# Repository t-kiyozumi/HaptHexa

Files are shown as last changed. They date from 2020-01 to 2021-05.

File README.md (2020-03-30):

# HaptHexa
The contents of this repository are the source code and design drawing of a 6-legged robot that can be operated using Dual Shock 3.

#Installation，How to use

Assemble the robot with reference to
HaptHexa / Hardware.

Clone the repository to the computer that controls the robot.

Create a build folder in 
HaptHexa / Software / mainDirectory /

After connecting the dual shock3 controller to the robot's control computer, 
enter the following command to execution

./HaptHexa

Use the left stick to move and the right stick to control the posture.
Pressing select activates the stabilizer and tries to keep the posture horizontal.
In this state, the right stick is used to control the center of gravity.

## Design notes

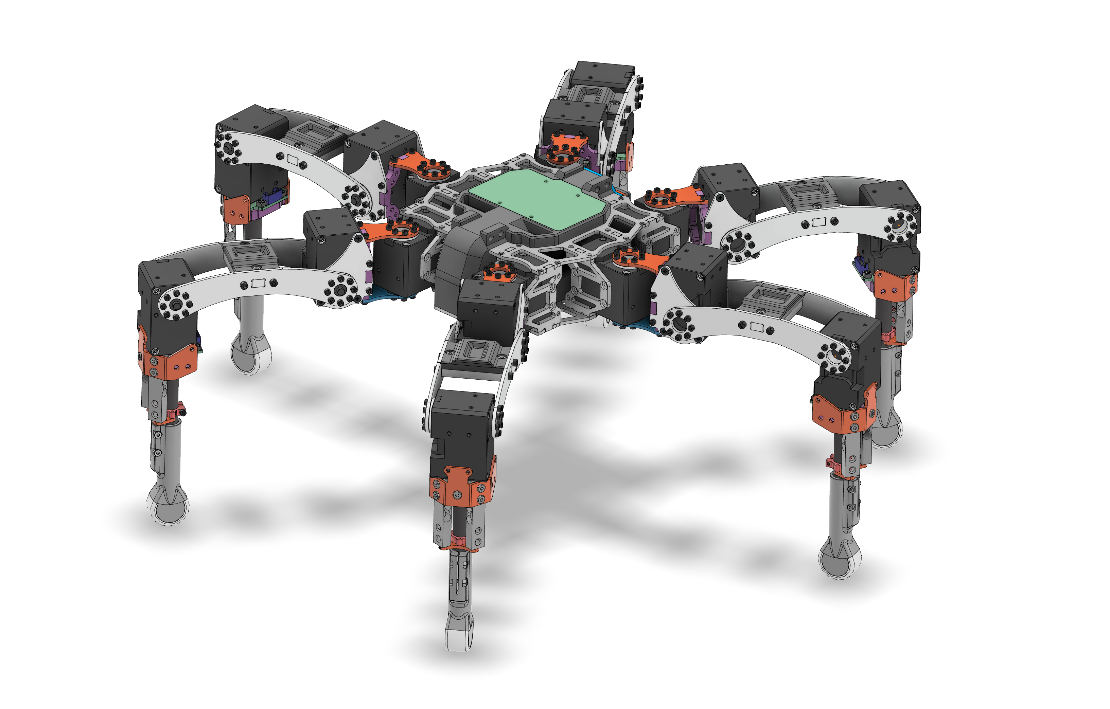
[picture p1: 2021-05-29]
Hardware/Inventor/00_000_HAPTHEXA_R3.png

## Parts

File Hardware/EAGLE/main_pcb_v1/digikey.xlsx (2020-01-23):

索引 | 数量 | 品番 | メーカー品番 | 商品概要 | 客先参照品番 | 入手可能 | 繰越注文 | 単価 | 合計金額 JPY
1 | 10 | WM1848-ND | 0436450500 | CONN RECEPT 5POS 3MM SINGLE ROW |  | 10 | 0 | 46.9 | 469
2 | 4 | WM1898CT-ND | 0436500513 | CONN HEADER 5POS R/A W/NAIL SMD |  | 4 | 0 | 344 | 1376
3 | 50 | WM1125CT-ND | 0430300002 | CONN TERM FEMALE 20-24AWG GOLD |  | 50 | 0 | 14.28 | 714

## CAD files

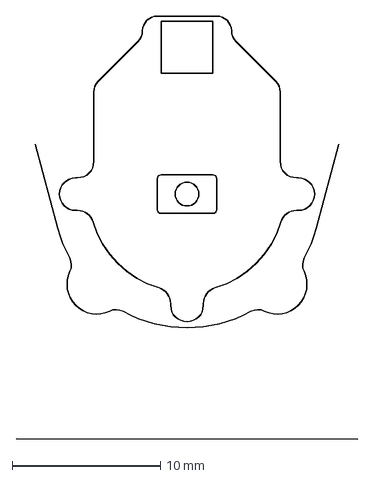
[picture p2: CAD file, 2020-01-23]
Hardware/EAGLE/force_sensor_pcb_v2/dxf/tplace_v2.dxf
23.0 x 28.5 mm

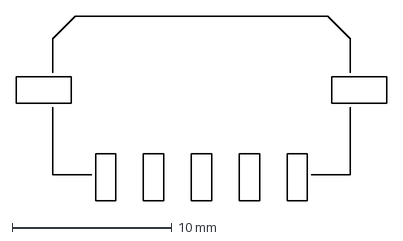
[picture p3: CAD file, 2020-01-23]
Hardware/EAGLE/main_pcb_v1/dxf/micro-fit 5.dxf
23.2 x 11.5 mm

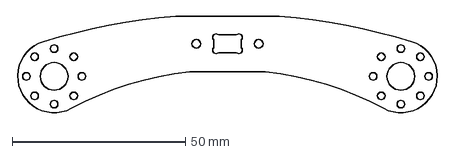
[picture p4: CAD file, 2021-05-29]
Hardware/Inventor/FEMUR_FRAME_DRIVER.dxf
122.0 x 28.5 mm

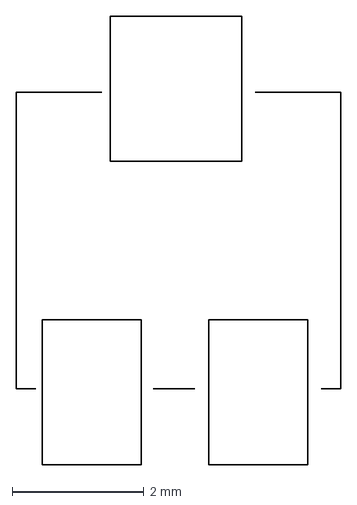
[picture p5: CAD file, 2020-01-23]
Hardware/EAGLE/force_sensor_pcb_v2/dxf/TOCOS G43A FOOTPRINT.dxf
4.92 x 6.80 mm

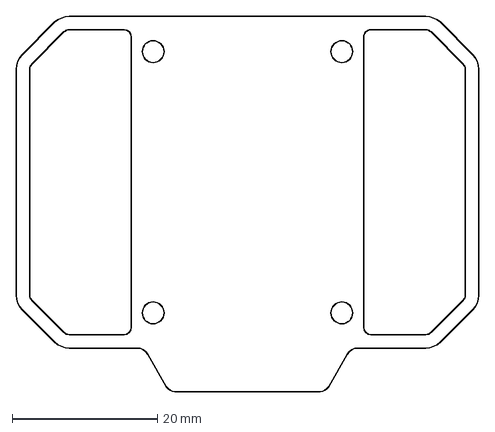
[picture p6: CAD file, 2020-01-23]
Hardware/EAGLE/main_pcb_v1/dxf/Dimention2.dxf
63.7 x 51.7 mm

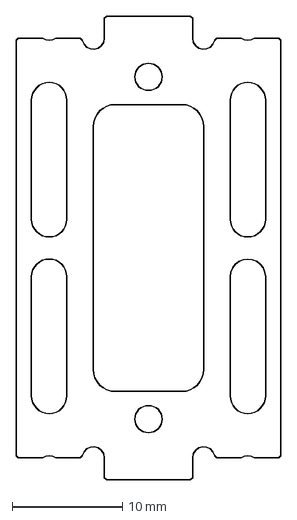
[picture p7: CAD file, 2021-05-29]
Hardware/Inventor/FEMUR_FRAME_BRIDGE.dxf
24.0 x 42.0 mm

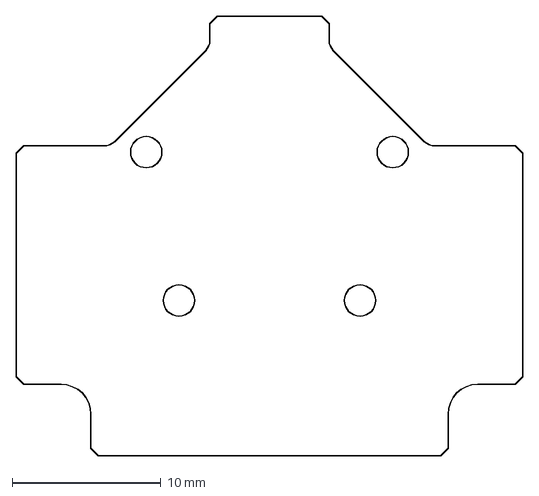
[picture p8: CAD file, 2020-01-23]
Hardware/EAGLE/force_sensor_pcb_v2/dxf/dimention_v2.dxf
34.0 x 29.5 mm

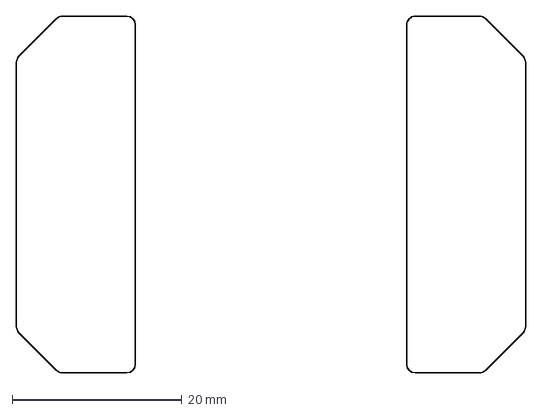
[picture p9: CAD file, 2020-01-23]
Hardware/EAGLE/main_pcb_v1/dxf/bPlace.dxf
60.0 x 42.0 mm

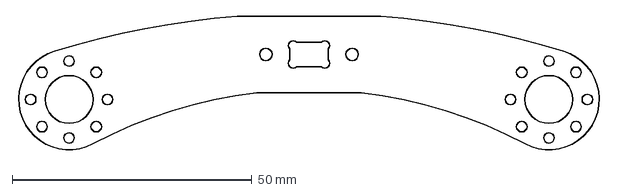
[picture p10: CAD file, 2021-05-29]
Hardware/Inventor/FEMUR_FRAME_FREE.dxf
122.0 x 28.5 mm

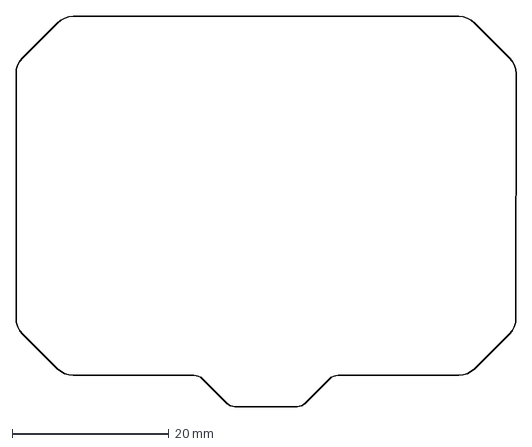
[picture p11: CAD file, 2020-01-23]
Hardware/EAGLE/main_pcb_v1/dxf/Dimention.dxf
63.8 x 49.8 mm

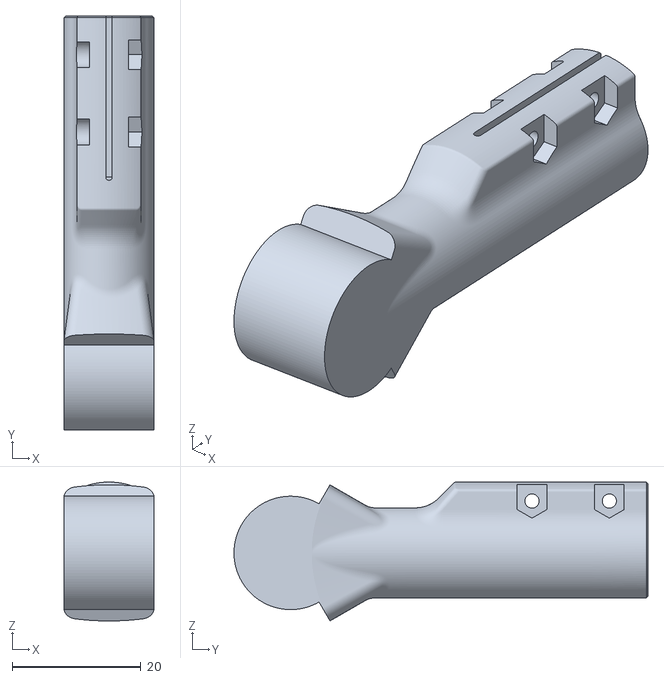
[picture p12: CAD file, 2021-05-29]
Hardware/Inventor/15_026_SHOE_GRIP_BASE_R3.stl
14.0 x 64.2 x 21.6

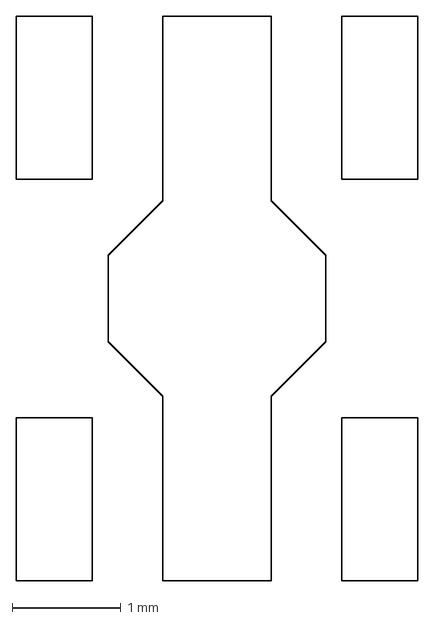
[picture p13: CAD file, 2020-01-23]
Hardware/EAGLE/main_pcb_v1/dxf/SOT-89-5.dxf
3.70 x 5.20 mm

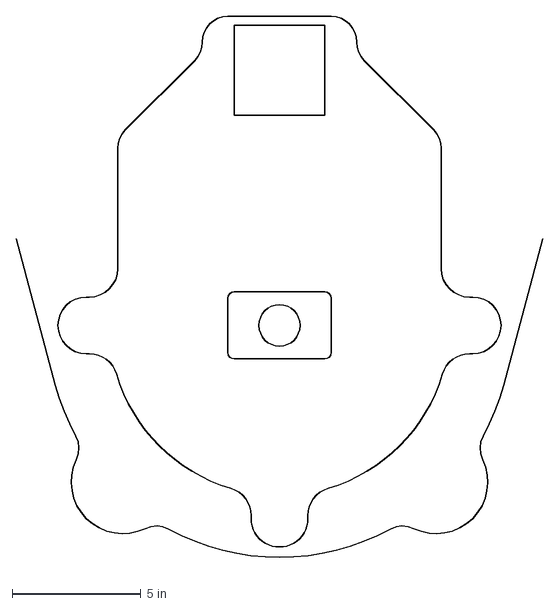
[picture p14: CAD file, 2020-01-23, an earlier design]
Hardware/EAGLE/force_sensor_pcb_v1/dxf/tplace.dxf
20.4 x 21.4 in

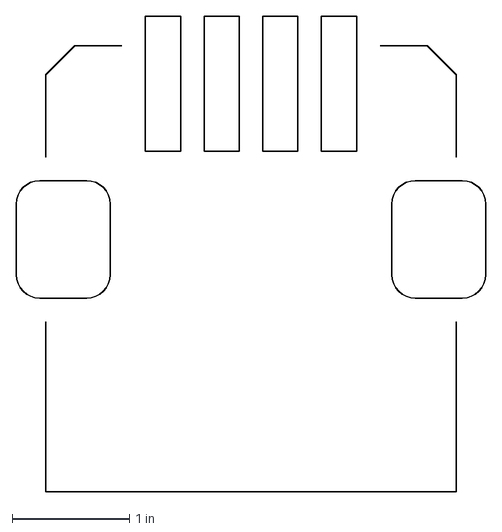
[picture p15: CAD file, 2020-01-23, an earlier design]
Hardware/EAGLE/force_sensor_pcb_v1/dxf/kyocera-6277 layout.dxf
4.00 x 4.05 in

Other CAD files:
Hardware/EAGLE/force_sensor_pcb_v1/dxf/HIROSE-DF58-4P.dxf
Hardware/EAGLE/force_sensor_pcb_v1/dxf/dimention.dxf
Hardware/Inventor/00_000_HAPTHEXA_R3.iam
Hardware/Inventor/00_002_SINGLE_LEG_R1.iam
Hardware/Inventor/00_003_COXA_R1.iam
Hardware/Inventor/00_004_FEMUR_R1.iam
Hardware/Inventor/00_005_TIBIA_R1.iam
Hardware/Inventor/00_015_FORCE_SENSOR_AMP_R1.iam
Hardware/Inventor/00_025_SHOE_R1.iam
Hardware/Inventor/00_031_THORAX_R1.iam
Hardware/Inventor/00_033_BATTERY_LIB_R1.iam
Hardware/Inventor/00_044_THORAX_YAW_R1.iam
Hardware/Inventor/00_052_LOADCELL_CONTACT_R1.iam
Hardware/Inventor/10_028_NYLON_NUT_M2_R1.ipt
Hardware/Inventor/10_036_BATTERY_COVER_BASE_R1.ipt
Hardware/Inventor/10_047_LOW_HEAD_SCREW_M2X5_R1.ipt
Hardware/Inventor/10_048_CAP_SCREW_M2X4_R1.ipt
Hardware/Inventor/10_049_FLAT_HEAD_SCREW_M2_5X15_R1.ipt
Hardware/Inventor/10_050_CAP_BOLT_M2X6_R1.ipt
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

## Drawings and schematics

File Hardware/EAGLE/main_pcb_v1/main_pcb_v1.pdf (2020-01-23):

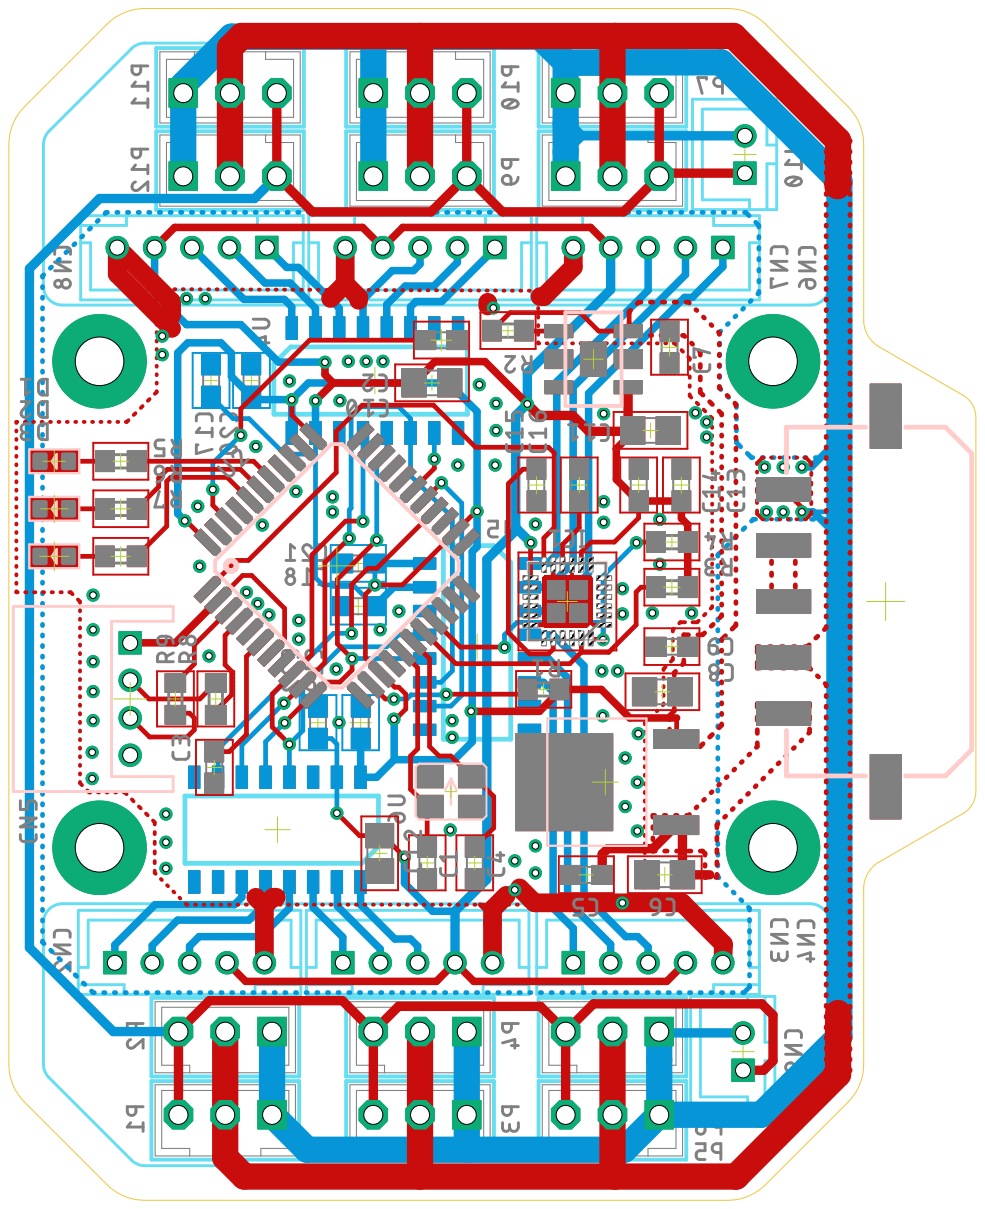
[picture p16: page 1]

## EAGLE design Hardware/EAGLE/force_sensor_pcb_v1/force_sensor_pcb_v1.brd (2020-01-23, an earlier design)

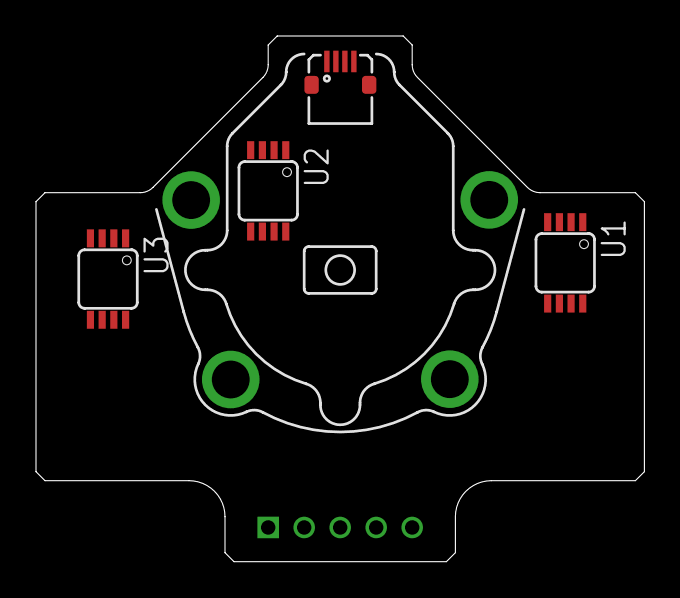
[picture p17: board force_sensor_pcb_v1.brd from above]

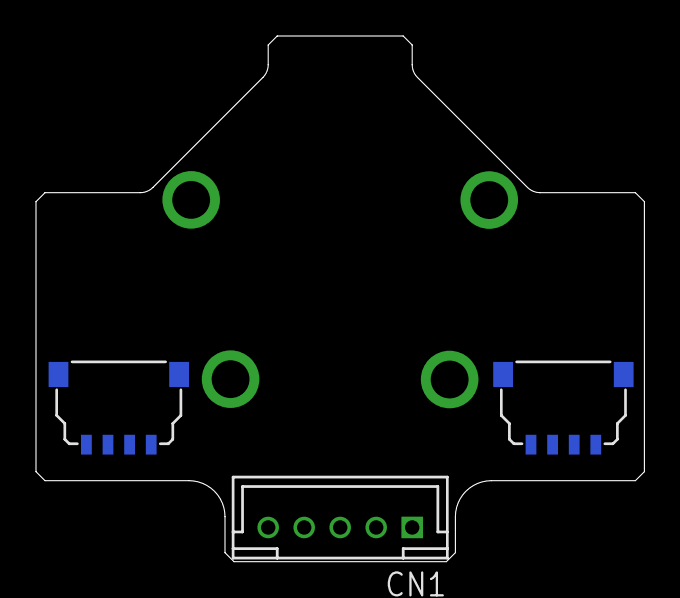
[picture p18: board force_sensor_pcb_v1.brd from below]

Board: 2 copper layers, 33.8 x 29.2 mm, 7 parts (3 on the bottom side), 2 nets, no tracks yet.

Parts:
CN1: B5B-PH-K-S
U1, U2, U3: AD623RM-8; MSOP08
U$1: KYOCERA-62774P; KYOCERA-6277-4
U$5, U$6: DF58-4P4P; DF58-4P

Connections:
+V: U1.7, U2.7, U3.7
-V: U1.4, U2.4, U3.4

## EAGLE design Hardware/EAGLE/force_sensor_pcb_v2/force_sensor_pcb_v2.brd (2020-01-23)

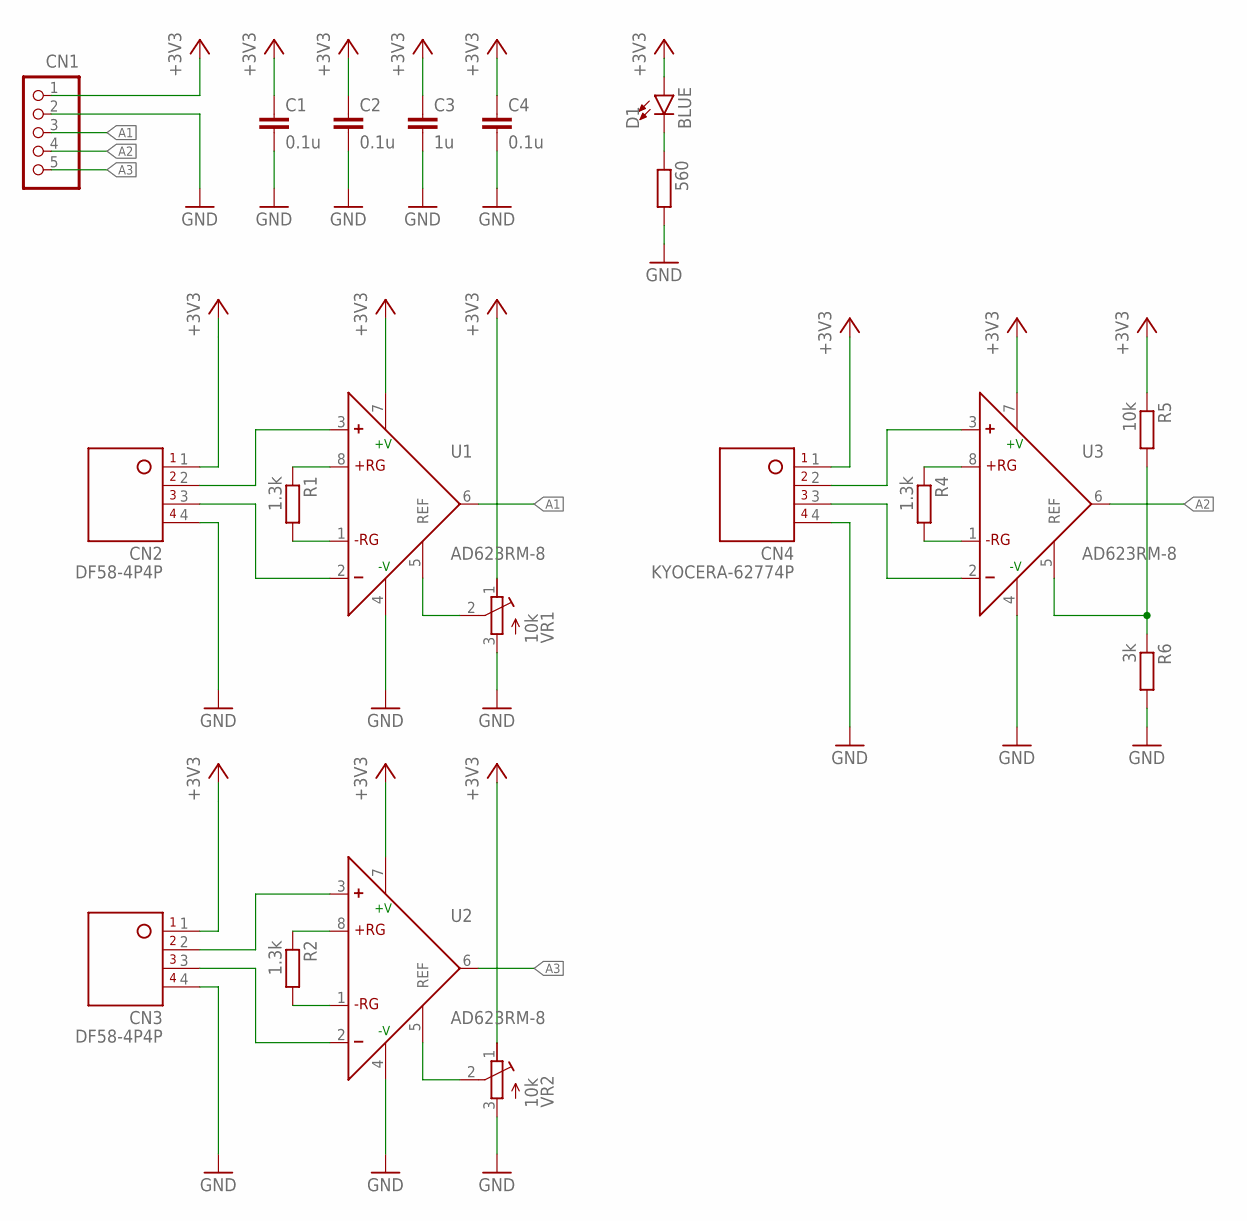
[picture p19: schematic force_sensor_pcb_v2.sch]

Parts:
560: R-EU_R0603; R0603
C1, C2, C4: 0.1u; C0603
C3: 1u; C0603
CN1: B5B-PH-K-S
CN2, CN3: DF58-4P4P; DF58-4P
CN4: KYOCERA-62774P; KYOCERA-6277-4
D1: BLUE; LED-0603
R1, R2, R4: 1.3k; R0603
R5: 10k; R0603
R6: 3k; R0603
U1, U2, U3: AD623RM-8; MSOP08
VR1, VR2: 10k; D43A

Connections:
+3V3: C1.1, C2.1, C3.1, C4.1, CN1.1, CN2.1, CN3.1, CN4.1, D1.A, R5.1, U1.7 (+V), U2.7 (+V), U3.7 (+V), VR1.1, VR2.1
A1: CN1.3, U1.6 (OUT)
A2: CN1.4, U3.6 (OUT)
A3: CN1.5, U2.6 (OUT)
GND: 560.2, C1.2, C2.2, C3.2, C4.2, CN1.2, CN2.4, CN3.4, CN4.4, R6.2, U1.4 (-V), U2.4 (-V), U3.4 (-V), VR1.3, VR2.3
unnamed: U1.5 (REF), VR1.2
unnamed: CN2.3, U1.2 (-IN)
unnamed: R1.1, U1.8 (+RG)
unnamed: R1.2, U1.1 (-RG)
unnamed: CN2.2, U1.3 (+IN)
unnamed: R2.1, U2.8 (+RG)
unnamed: U2.5 (REF), VR2.2
unnamed: CN3.3, U2.2 (-IN)
unnamed: CN3.2, U2.3 (+IN)
unnamed: R2.2, U2.1 (-RG)
unnamed: R4.1, U3.8 (+RG)
unnamed: R5.2, R6.1, U3.5 (REF)
unnamed: CN4.3, U3.2 (-IN)
unnamed: CN4.2, U3.3 (+IN)
unnamed: R4.2, U3.1 (-RG)
unnamed: 560.1, D1.C

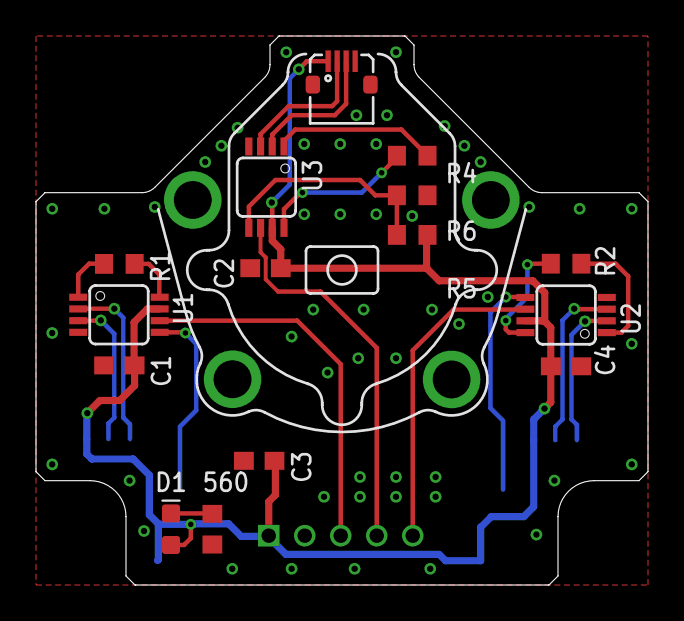
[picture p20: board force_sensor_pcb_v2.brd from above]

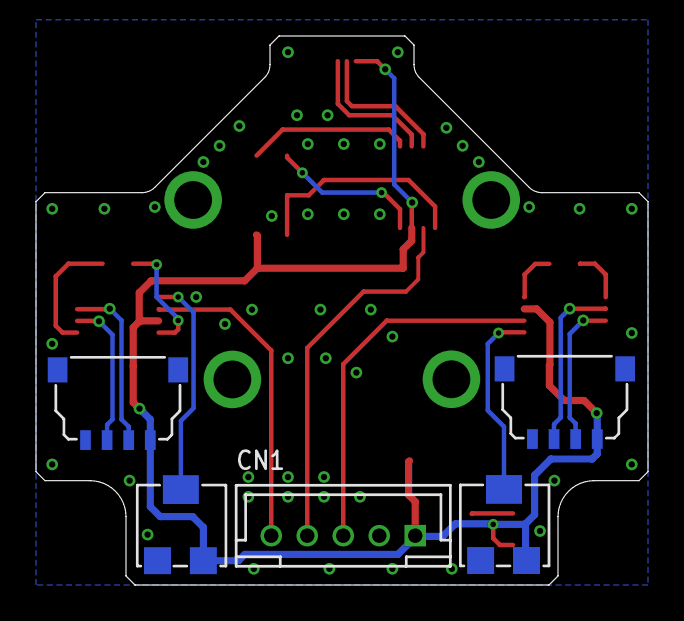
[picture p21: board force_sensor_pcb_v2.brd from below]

Board: 2 copper layers, 34.0 x 30.5 mm, 20 parts (5 on the bottom side), 21 nets.

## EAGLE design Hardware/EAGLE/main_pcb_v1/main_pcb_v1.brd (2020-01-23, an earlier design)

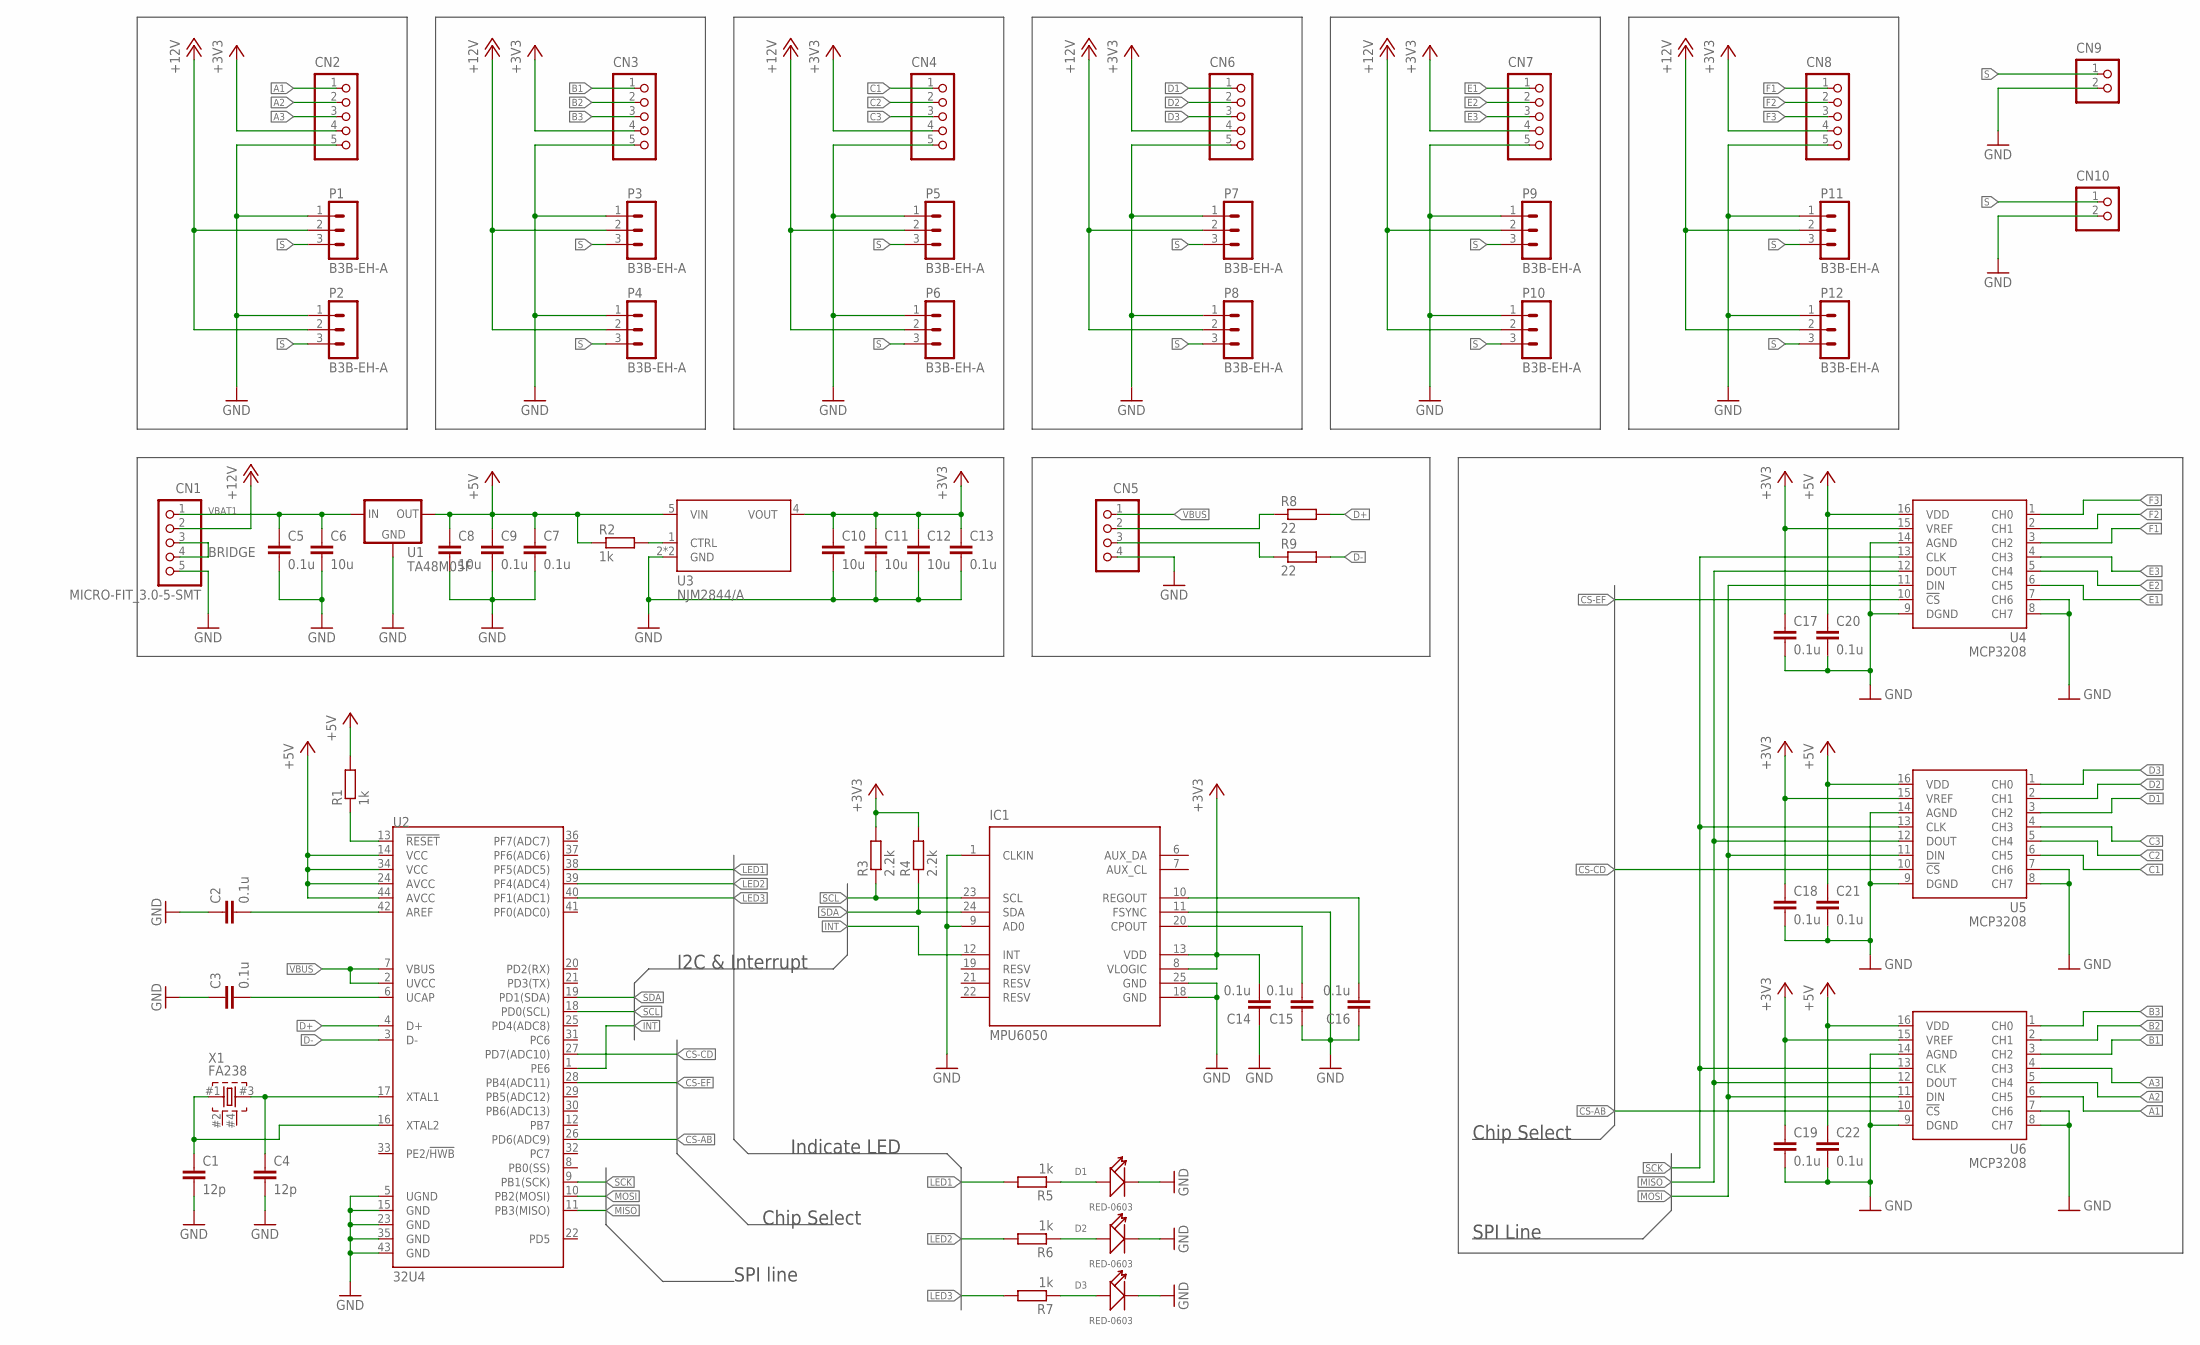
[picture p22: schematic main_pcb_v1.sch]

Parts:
C1, C4: 12p; C0603
C2, C3, C5, C7, C9, C13, C14, C15, C16, C17, C18, C19, C20, C21, C22: 0.1u; C0603
C6, C8, C10, C11, C12: 10u; C0805
CN1: MICRO-FIT_3.0-5-SMT; MICRO-FIT_3.0-5_SMT
CN2, CN3, CN4, CN6, CN7, CN8: B5B-PH-K-S
CN5: S4B-PH-K-S
CN9, CN10: B2B-PH-K-S
D1, D2, D3: RED-0603; LED-0603
IC1: MPU6050; QFN50P400X400X95-25T265X275N
P1, P2, P3, P4, P5, P6, P7, P8, P9, P10, P11, P12: B3B-EH-A
R1, R2, R5, R6, R7: 1k; R0603
R3, R4: 2.2k; R0603
R8, R9: 22; R0603
U1: TA48M05F; HSOP3-P-2.30A
U2: 32U4; TQFP44
U3: NJM2844/A; SOT-89-5
U4, U5, U6: MCP3208; SO16
X1: FA238; OSC-FA238

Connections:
+3V3: C10.1, C11.1, C12.1, C13.1, C14.2, C17.1, C18.1, C19.1, CN2.4, CN3.4, CN4.4, CN6.4, CN7.4, CN8.4, IC1.8 (VLOGIC), IC1.13 (VDD), R3.2, R4.2, U3.4 (VOUT), U4.15 (VREF), U5.15 (VREF), U6.15 (VREF)
+5V: C7.1, C8.1, C9.1, C20.1, C21.1, C22.1, R1.2, R2.1, U1.2 (OUT), U2.14 (VCC), U2.24 (AVCC), U2.34 (VCC), U2.44 (AVCC), U3.5 (VIN), U4.16 (VDD), U5.16 (VDD), U6.16 (VDD)
+12V: CN1.2, P1.2, P2.2, P3.2, P4.2, P5.2, P6.2, P7.2, P8.2, P9.2, P10.2, P11.2, P12.2
A1: CN2.1, U6.6 (CH5)
A2: CN2.2, U6.5 (CH4)
A3: CN2.3, U6.4 (CH3)
B1: CN3.1, U6.3 (CH2)
B2: CN3.2, U6.2 (CH1)
B3: CN3.3, U6.1 (CH0)
BRIDGE: CN1.3, CN1.4
C1: CN4.1, U5.6 (CH5)
C2: CN4.2, U5.5 (CH4)
C3: CN4.3, U5.4 (CH3)
CS-AB: U2.26 (PD6(ADC9)), U6.10 (!CS)
CS-CD: U2.27 (PD7(ADC10)), U5.10 (!CS)
CS-EF: U2.28 (PB4(ADC11)), U4.10 (!CS)
D1: CN6.1, U5.3 (CH2)
D2: CN6.2, U5.2 (CH1)
D3: CN6.3, U5.1 (CH0)
D+: R8.2, U2.4 (D+)
D-: R9.2, U2.3 (D-)
E1: CN7.1, U4.6 (CH5)
E2: CN7.2, U4.5 (CH4)
E3: CN7.3, U4.4 (CH3)
F1: CN8.1, U4.3 (CH2)
F2: CN8.2, U4.2 (CH1)
F3: CN8.3, U4.1 (CH0)
GND: C1.2, C2.1, C3.1, C4.2, C5.2, C6.2, C7.2, C8.2, C9.2, C10.2, C11.2, C12.2, C13.2, C14.1, C15.1, C16.1, C17.2, C18.2, C19.2, C20.2, C21.2, C22.2, CN1.5, CN2.5, CN3.5, CN4.5, CN5.4, CN6.5, CN7.5, CN8.5, CN9.2, CN10.2, D1.-, D2.-, D3.-, IC1.1 (CLKIN), IC1.9 (AD0), IC1.11 (FSYNC), IC1.18 (GND), IC1.25 (GND), P1.1, P2.1, P3.1, P4.1, P5.1, P6.1, P7.1, P8.1, P9.1, P10.1, P11.1, P12.1, U1.3 (GND), U2.5 (UGND), U2.15 (GND), U2.23 (GND), U2.35 (GND), U2.43 (GND), U3.2 (GND), U3.2' (GND), U4.7 (CH6), U4.8 (CH7), U4.9 (DGND), U4.14 (AGND), U5.7 (CH6), U5.8 (CH7), U5.9 (DGND), U5.14 (AGND), U6.7 (CH6), U6.8 (CH7), U6.9 (DGND), U6.14 (AGND)
INT: IC1.12 (INT), U2.1 (PE6)
LED1: R5.2, U2.38 (PF5(ADC5))
LED2: R6.2, U2.39 (PF4(ADC4))
LED3: R7.2, U2.40 (PF1(ADC1))
MISO: U2.11 (PB3(MISO)), U4.12 (DOUT), U5.12 (DOUT), U6.12 (DOUT)
MOSI: U2.10 (PB2(MOSI)), U4.11 (DIN), U5.11 (DIN), U6.11 (DIN)
unnamed: CN5.2, R8.1
unnamed: CN5.3, R9.1
unnamed: R2.2, U3.1 (CTRL)
unnamed: C4.1, U2.17 (XTAL1), X1.#3 (3)
unnamed: C1.1, U2.16 (XTAL2), X1.#1 (1)
unnamed: C3.2, U2.6 (UCAP)
unnamed: R1.1, U2.13 (!RESET)
unnamed: C2.2, U2.42 (AREF)
unnamed: C16.2, IC1.10 (REGOUT)
unnamed: D3.+, R7.1
unnamed: C15.2, IC1.20 (CPOUT)
unnamed: D2.+, R6.1
unnamed: D1.+, R5.1
S: CN9.1, CN10.1, P1.3, P2.3, P3.3, P4.3, P5.3, P6.3, P7.3, P8.3, P9.3, P10.3, P11.3, P12.3
SCK: U2.9 (PB1(SCK)), U4.13 (CLK), U5.13 (CLK), U6.13 (CLK)
SCL: IC1.23 (SCL), R3.1, U2.18 (PD0(SCL))
SDA: IC1.24 (SDA), R4.1, U2.19 (PD1(SDA))
VBAT1: C5.1, C6.1, CN1.1, U1.1 (IN)
VBUS: CN5.1, U2.2 (UVCC), U2.7 (VBUS)

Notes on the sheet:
Chip Select
SPI Line
SPI line
Indicate LED
I2C & Interrupt

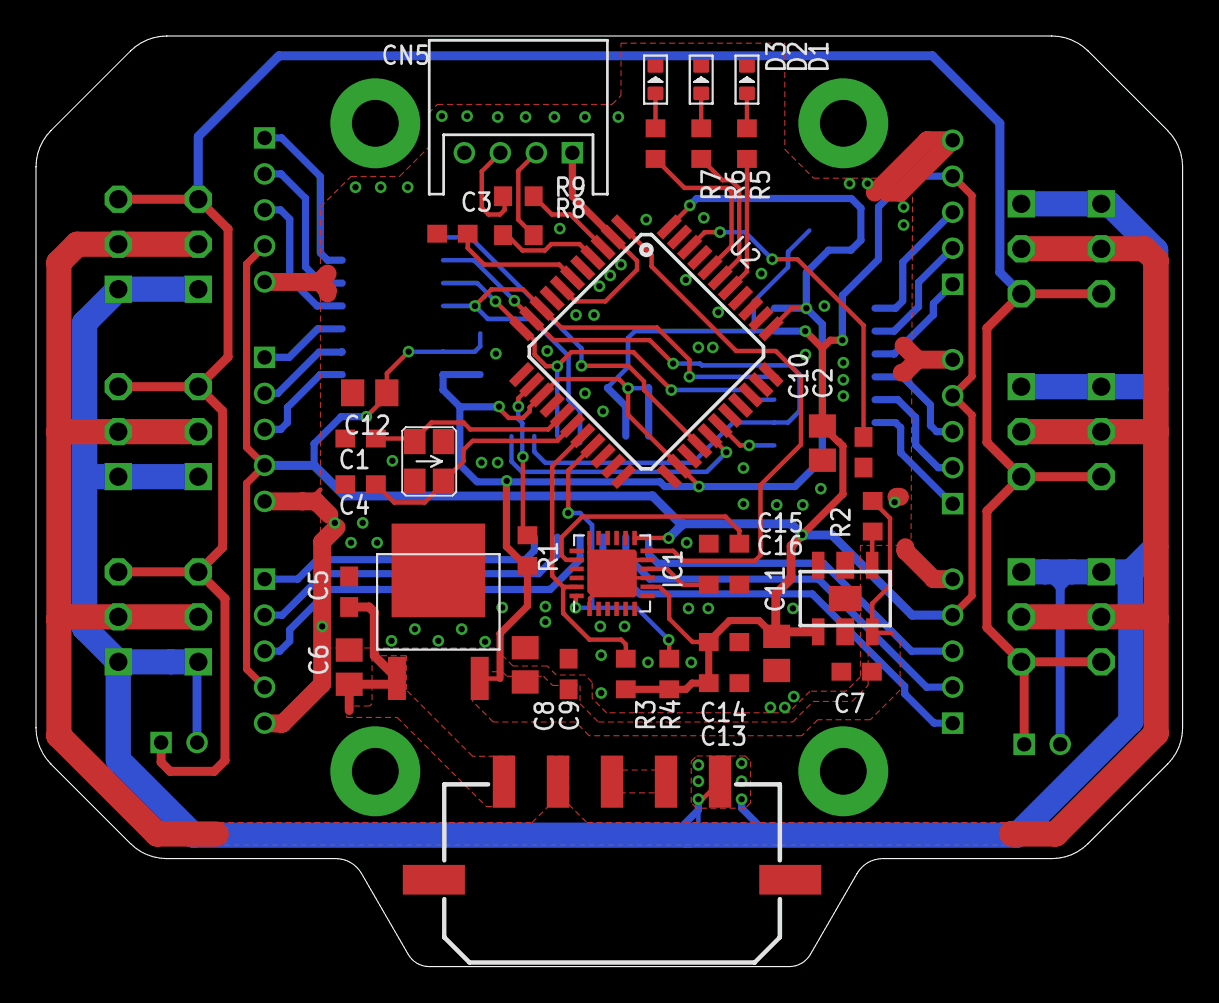
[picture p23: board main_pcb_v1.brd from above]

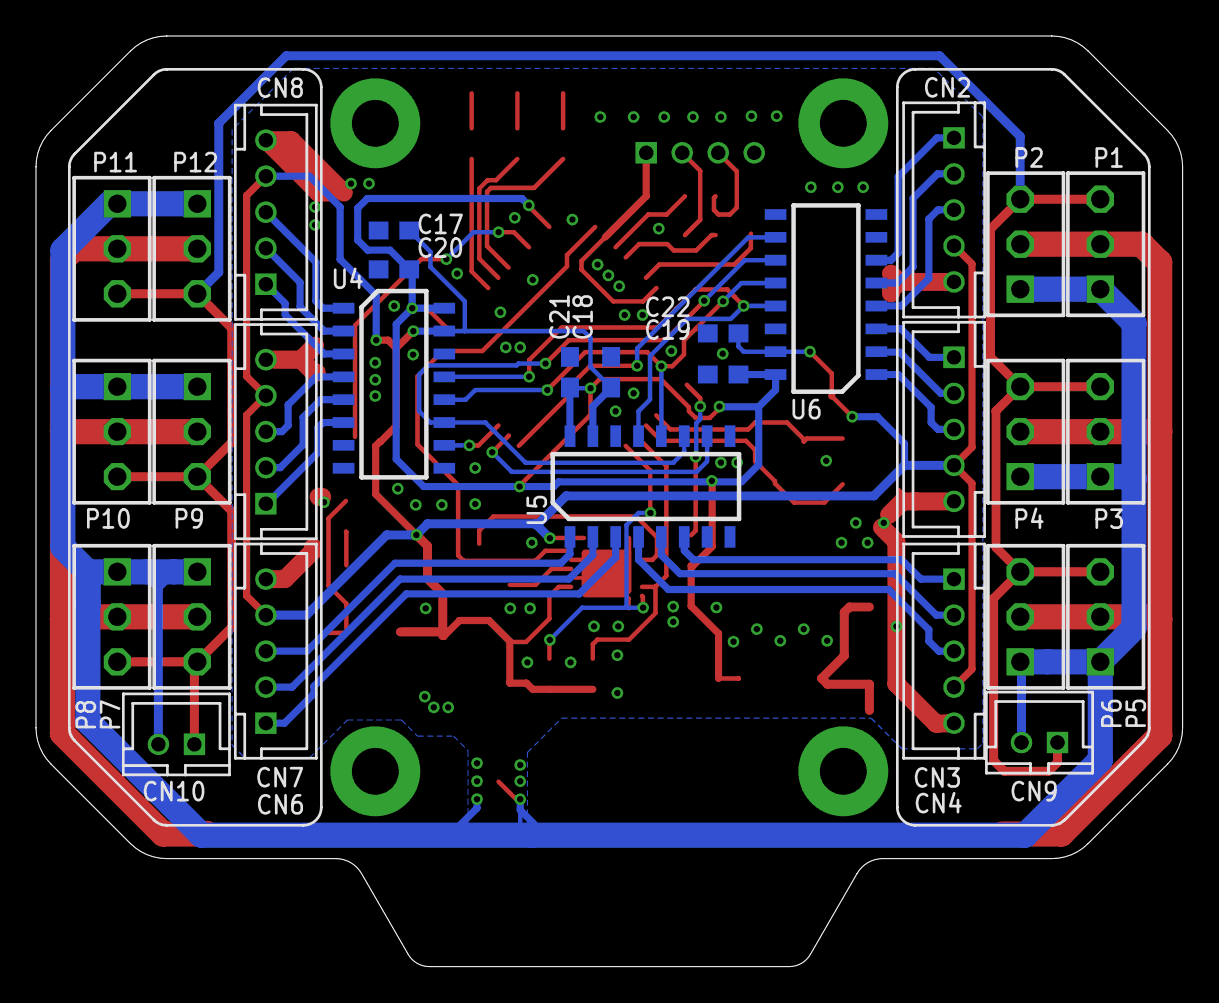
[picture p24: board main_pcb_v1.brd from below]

Board: 2 copper layers, 63.7 x 51.7 mm, 64 parts (29 on the bottom side), 53 nets.

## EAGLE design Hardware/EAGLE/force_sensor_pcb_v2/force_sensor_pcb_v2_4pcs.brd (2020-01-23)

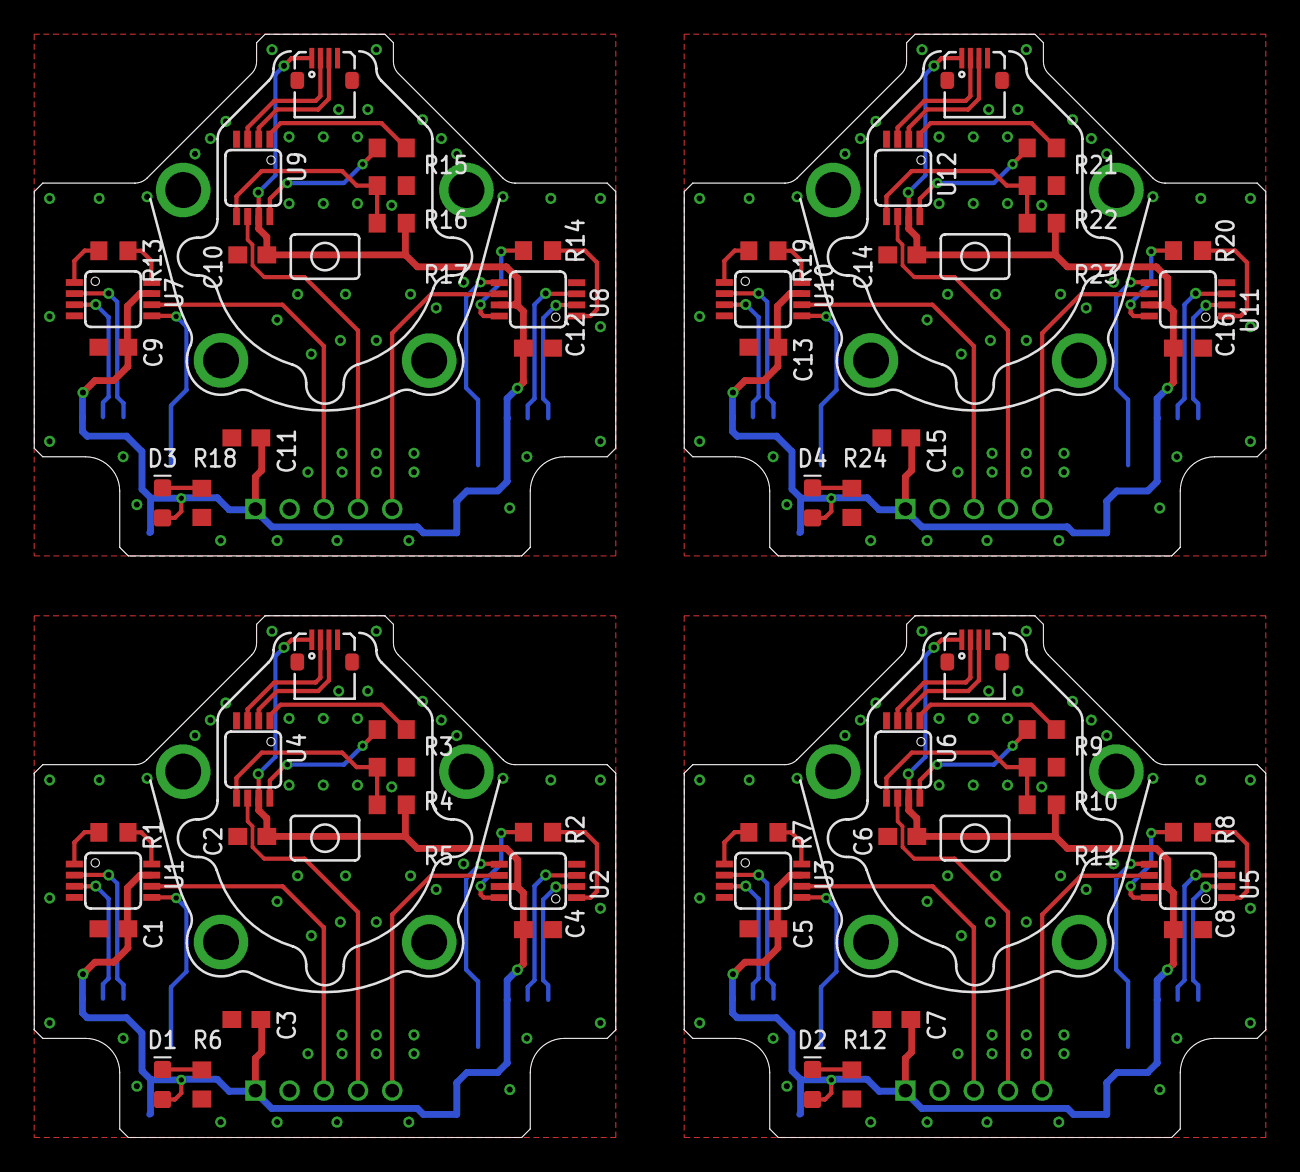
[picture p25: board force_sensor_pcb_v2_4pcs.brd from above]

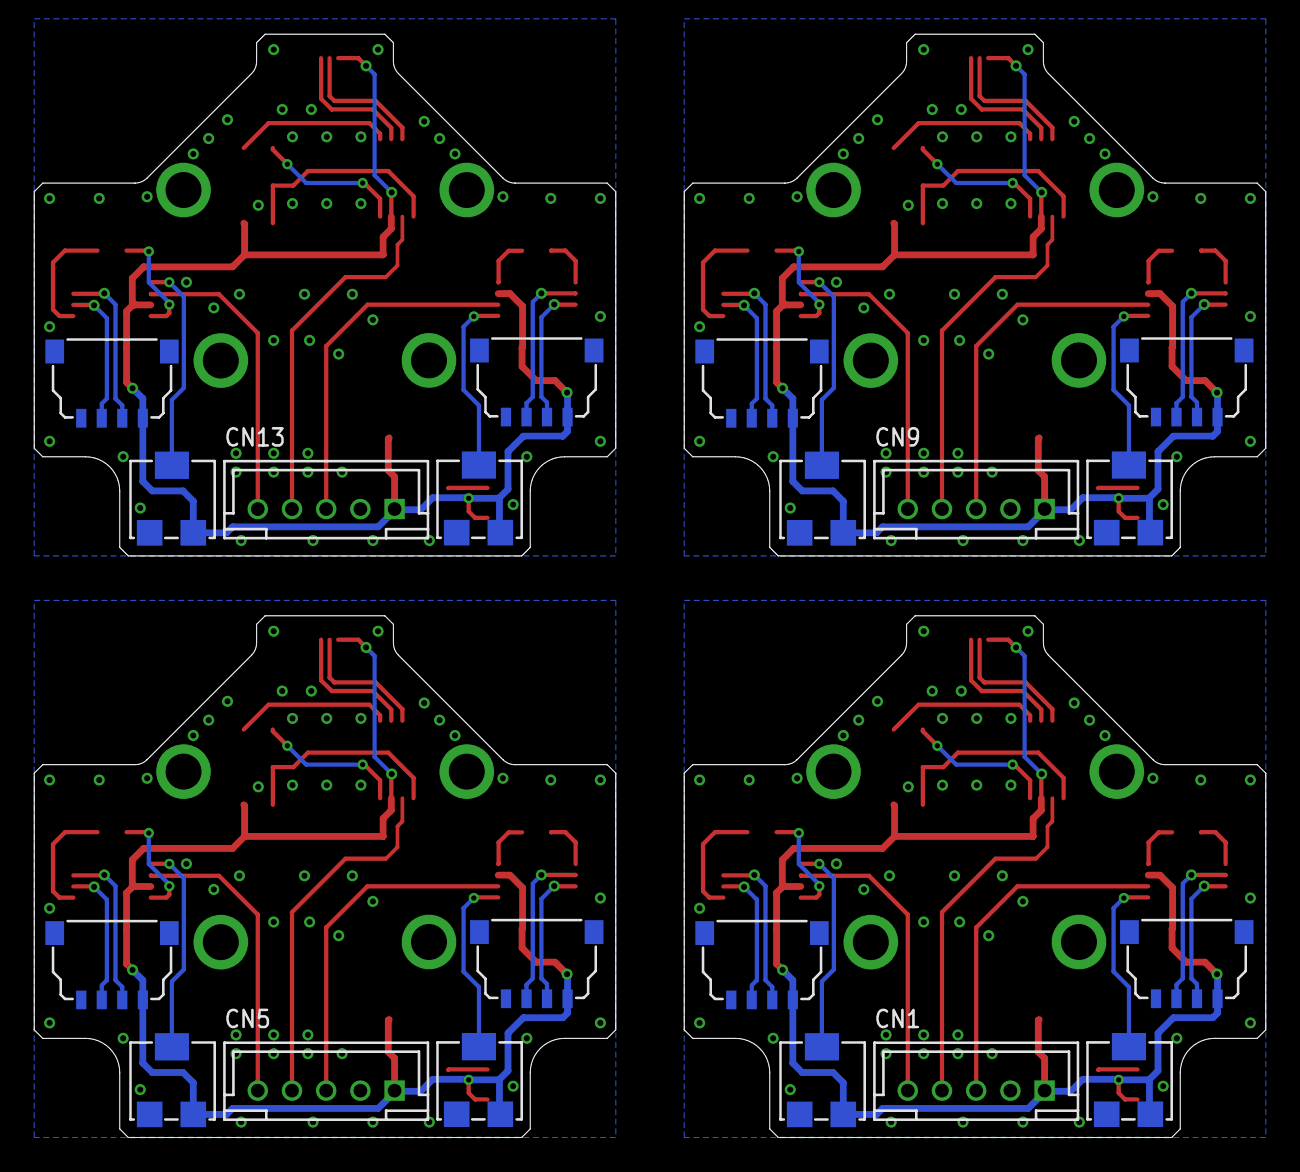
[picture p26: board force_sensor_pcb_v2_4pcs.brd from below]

Board: 2 copper layers, 72.0 x 64.5 mm, 80 parts (20 on the bottom side), 84 nets.

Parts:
C1, C2, C3, C4, C5, C6, C7, C8, C9, C10, C11, C12, C13, C14, C15, C16: C0603
CN1, CN5, CN9, CN13: B5B-PH-K-S
CN2, CN3, CN6, CN8, CN10, CN12, CN14, CN16: DF58-4P4P; DF58-4P
CN4, CN7, CN11, CN15: KYOCERA-62774P; KYOCERA-6277-4
D1, D2, D3, D4: BLUE; LED-0603
R1, R2, R6, R7, R8, R12, R13, R14, R18, R19, R20, R24: R0603
R3, R9, R15, R21: 1.3k; R0603
R4, R10, R16, R22: 3k; R0603
R5, R11, R17, R23: 10k; R0603
U1, U2, U3, U4, U5, U6, U7, U8, U9, U10, U11, U12: AD623RM-8; MSOP08
VR1, VR2, VR3, VR4, VR5, VR6, VR7, VR8: D43A

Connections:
+3V1: C5.1, C6.1, C7.1, C8.1, CN5.1, CN6.1, CN7.1, CN8.1, D2.A, R11.1, U3.7, U5.7, U6.7, VR3.1, VR4.1
+3V2: C9.1, C10.1, C11.1, C12.1, CN9.1, CN10.1, CN11.1, CN12.1, D3.A, R17.1, U7.7, U8.7, U9.7, VR5.1, VR6.1
+3V3: C1.1, C2.1, C3.1, C4.1, CN1.1, CN2.1, CN3.1, CN4.1, D1.A, R5.1, U1.7, U2.7, U4.7, VR1.1, VR2.1
+3V4: C13.1, C14.1, C15.1, C16.1, CN13.1, CN14.1, CN15.1, CN16.1, D4.A, R23.1, U10.7, U11.7, U12.7, VR7.1, VR8.1
A1: CN1.3, U1.6
A2: CN1.4, U4.6
A3: CN1.5, U2.6
A4: CN5.3, U3.6
A5: CN5.4, U6.6
A6: CN5.5, U5.6
A7: CN9.3, U7.6
A8: CN9.4, U9.6
A9: CN9.5, U8.6
A10: CN13.3, U10.6
A11: CN13.4, U12.6
A12: CN13.5, U11.6
GND: C1.2, C2.2, C3.2, C4.2, CN1.2, CN2.4, CN3.4, CN4.4, R4.2, R6.2, U1.4, U2.4, U4.4, VR1.3, VR2.3
GND1: C5.2, C6.2, C7.2, C8.2, CN5.2, CN6.4, CN7.4, CN8.4, R10.2, R12.2, U3.4, U5.4, U6.4, VR3.3, VR4.3
GND2: C9.2, C10.2, C11.2, C12.2, CN9.2, CN10.4, CN11.4, CN12.4, R16.2, R18.2, U7.4, U8.4, U9.4, VR5.3, VR6.3
GND3: C13.2, C14.2, C15.2, C16.2, CN13.2, CN14.4, CN15.4, CN16.4, R22.2, R24.2, U10.4, U11.4, U12.4, VR7.3, VR8.3
unnamed: U1.5, VR1.2
unnamed: CN2.3, U1.2
unnamed: R1.1, U1.8
unnamed: R1.2, U1.1
unnamed: CN2.2, U1.3
unnamed: R2.1, U2.8
unnamed: U2.5, VR2.2
unnamed: CN3.3, U2.2
unnamed: CN3.2, U2.3
unnamed: R2.2, U2.1
unnamed: R3.1, U4.8
unnamed: R4.1, R5.2, U4.5
unnamed: CN4.3, U4.2
unnamed: CN4.2, U4.3
unnamed: R3.2, U4.1
unnamed: D1.C, R6.1
unnamed: R7.1, U3.8
unnamed: U3.5, VR3.2
unnamed: CN6.3, U3.2
unnamed: CN6.2, U3.3
unnamed: R7.2, U3.1
unnamed: R8.1, U5.8
unnamed: U5.5, VR4.2
unnamed: CN8.3, U5.2
unnamed: CN8.2, U5.3
unnamed: R8.2, U5.1
unnamed: R9.1, U6.8
unnamed: R10.1, R11.2, U6.5
unnamed: CN7.3, U6.2
unnamed: CN7.2, U6.3
unnamed: R9.2, U6.1
unnamed: D2.C, R12.1
unnamed: R13.1, U7.8
unnamed: U7.5, VR5.2
unnamed: CN10.3, U7.2
unnamed: CN10.2, U7.3
unnamed: R13.2, U7.1
unnamed: R14.1, U8.8
unnamed: U8.5, VR6.2
unnamed: CN12.3, U8.2
unnamed: CN12.2, U8.3
unnamed: R14.2, U8.1
unnamed: R15.1, U9.8
unnamed: R16.1, R17.2, U9.5
unnamed: CN11.3, U9.2
unnamed: CN11.2, U9.3
unnamed: R15.2, U9.1
unnamed: D3.C, R18.1
unnamed: R19.1, U10.8
unnamed: U10.5, VR7.2
unnamed: CN14.3, U10.2
unnamed: CN14.2, U10.3
unnamed: R19.2, U10.1
unnamed: R20.1, U11.8
unnamed: U11.5, VR8.2
unnamed: CN16.3, U11.2
unnamed: CN16.2, U11.3
unnamed: R20.2, U11.1
unnamed: R21.1, U12.8
unnamed: R22.1, R23.2, U12.5
unnamed: CN15.3, U12.2
unnamed: CN15.2, U12.3
unnamed: R21.2, U12.1
unnamed: D4.C, R24.1

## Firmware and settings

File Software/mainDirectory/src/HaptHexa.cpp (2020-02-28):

#include <DynamixelWorkbench.h>
#include <stdio.h>
#include <string.h>
#include <math.h>
#include <time.h>
#include <unistd.h>
#include <ncurses.h>

DynamixelWorkbench dxl_wb;

#include <fcntl.h>
#include <stdio.h>
#include <stdlib.h>
#include <linux/joystick.h>
#include <string>
#include <errno.h>   // Error integer and strerror() function
#include <termios.h> // Contains POSIX terminal control definitions
#include <unistd.h>  // write(), read(), close()
#include <sys/time.h>

enum leg_num
{
  front_right,
  middle_right,
  rear_right,
  rear_left,
  middle_left,
  front_left,
};

class PID_parm
{
public:
  double DELTA_T;
  double KP = 2.50;
  double KD = 0.0001;
  double KI = 50.0;
  double int_err = 0.0;
  double dif[2];
  double currentTime;
  double pastTime;
};
class support_polygon
{
public:
  double long_diagonal = 44;
  double short_diagonal = 22 * sqrt(3.0);
  double side = 22;
};

enum mode
{
  auto_attitude_mode,
  manualMode,
};

class hexapod_body_state
{
public:
  const double side = 8.0, long_diagonal = 16.0, short_diagonal = 8 * sqrt(3.0);
  double yaw = 0.0, pitch = 0.0, roll = 0.0;
  double cog_height = 12.5;
  double ZMP_x, ZMP_y;
  int mode = manualMode;
  int mode_is_alrdy_changed;
};

class jy901_state
{
public:
  double yaw = 0.0;
  double roll = 0.0;
  double pich = 0.0;
  double accX;
  double accY;
  double accZ;
  double roll_offset = 0.0;
  double pitch_offset = 0.0;
  int is_calibration = 0;
};

class leg_state
{
public:
  const double coxa_length = 4, femur_length = 10, tibia_length = 12.5;
  int32_t coxa_encoder_val, femur_encoder_val, tibia_encoder_val; //value that order to encoder between 0 - 4048
  double coxa_arg, femur_arg, tibia_arg;                          //argument of joint -π[rad]〜+π[rad]
  double dx = 0.0, dy = 0.0, dz = 0.0;
  double x, y, z;
  double dx_home = 0.0, dy_home = 0.0, dz_home = 0.0;
  double x_home = 0.0, y_home = 0.0, z_home = 0.0;
  double x_base, y_base, z_base;
  double trajectory_hight = 10.0, trajectory_width = 5.0;
  double trajectory_yaw = 0.0, trajectory_pitch = 0.0;
  double trajectory_velocity;
};

typedef struct
{
  uint16_t X;
  uint16_t Y;
  uint16_t A;
  uint16_t B;
  uint16_t LB;
  uint16_t LT;
  uint16_t RB;
  uint16_t RT;
  uint16_t start;
  uint16_t back;
  int16_t axes1_x;
  int16_t axes1_y;
  int16_t axes0_x;
  int16_t axes0_y;
} controler_state;

void write_controler_state(controler_state *controler, js_event event)
{
  switch (event.type)
  {
  case JS_EVENT_BUTTON:
    if (event.number == 1)
    {
      controler->A = event.value;
    }
    if (event.number == 2)
    {
      controler->B = event.value;
    }
    if (event.number == 0)
    {
      controler->X = event.value;
    }
    if (event.number == 3)
    {
      controler->Y = event.value;
    }
    if (event.number == 4)
    {
      controler->LB = event.value;
    }
    if (event.number == 5)
    {
      controler->RB = event.value;
    }
    if (event.number == 6)
    {
      controler->LT = event.value;
    }
    if (event.number == 7)
    {
      controler->RT = event.value;
    }
    if (event.number == 9)
    {
      controler->start = event.value;
    }
    if (event.number == 0)
    {
      controler->X = event.value;
    }
    if (event.number == 3)
    {
      controler->Y = event.value;
    }
    if (event.number == 8)
    {
      controler->back = event.value;
      // printf("bock %d", controler->back);
    }

    break;
  case JS_EVENT_AXIS:
    if (event.number == 0)
    {
      controler->axes0_x = event.value;
    }
    if (event.number == 1)
    {
      controler->axes0_y = -event.value;
    }
    if (event.number == 2)
    {
      controler->axes1_x = event.value;
    }
    if (event.number == 3)
    {
      controler->axes1_y = -event.value;
    }
    break;
  default:
    /* Ignore init events. */
    break;
  }
}

void rotate_trajectory_depending_joy(leg_state *tmp_leg, hexapod_body_state *tmp_body_state, support_polygon *support_hexagon, controler_state *controler, double count)
{ //this is open loop controll as test

  int j = front_left;
  double delta_yaw;
  if (controler->LB || controler->RB)
  {
    if (controler->RB)
    {
      delta_yaw = (M_PI / 18.0) * sin(count * M_PI * 2 * 0.0020125);
    }
    if (controler->LB)
    {
      delta_yaw = -(M_PI / 18.0) * sin(count * M_PI * 2 * 0.0020125);
    }

    // int k = middle_right;
    for (int i = 0; i <= j; i++)
    {

      if (i == front_left)
      {
        tmp_leg[i].x = (0.5 * support_hexagon->long_diagonal * sin((M_PI / 3.0) + delta_yaw) - 0.5 * tmp_body_state->short_diagonal);
        tmp_leg[i].y = -(0.5 * support_hexagon->long_diagonal * cos((M_PI / 3.0) + delta_yaw) - 0.5 * tmp_body_state->side);
        tmp_leg[i].z = tmp_leg[i].z_home + 3 * cos(count * M_PI * 2 * 0.0020125);
        if (tmp_leg[i].z <= tmp_leg[i].z_home)
        {
          tmp_leg[i].z = tmp_leg[i].z_home;
        }
      }
      if (i == middle_right)
      {
        tmp_leg[i].x = 0.5 * support_hexagon->long_diagonal * cos(delta_yaw) - 0.5 * tmp_body_state->long_diagonal;
        tmp_leg[i].y = 0.5 * support_hexagon->long_diagonal * sin(delta_yaw);
        tmp_leg[i].z = tmp_leg[i].z_home + 3 * cos(count * M_PI * 2 * 0.0020125);
        if (tmp_leg[i].z <= tmp_leg[i].z_home)
        {
          tmp_leg[i].z = tmp_leg[i].z_home;
        }
      }
      if (i == rear_left)
      {
        tmp_leg[i].x = (0.5 * support_hexagon->long_diagonal * sin((M_PI / 3.0) - delta_yaw) - 0.5 * tmp_body_state->short_diagonal);
        tmp_leg[i].y = (0.5 * support_hexagon->long_diagonal * cos((M_PI / 3.0) - delta_yaw) - 0.5 * tmp_body_state->side);
        tmp_leg[i].z = tmp_leg[i].z_home + 3 * cos(count * M_PI * 2 * 0.0020125);
        if (tmp_leg[i].z <= tmp_leg[i].z_home)
        {
          tmp_leg[i].z = tmp_leg[i].z_home;
        }
      }

      //////////////////////////////////////////////////////////////////////////////////////////////////////////////////////////////////
      if (i == rear_right)
      {
        tmp_leg[i].x = (0.5 * support_hexagon->long_diagonal * sin((M_PI / 3.0) - delta_yaw) - 0.5 * tmp_body_state->short_diagonal);
        tmp_leg[i].y = -(0.5 * support_hexagon->long_diagonal * cos((M_PI / 3.0) - delta_yaw) - 0.5 * tmp_body_state->side);
        tmp_leg[i].z = tmp_leg[i].z_home - 3 * cos(count * M_PI * 2 * 0.0020125);
        if (tmp_leg[i].z <= tmp_leg[i].z_home)
        {
          tmp_leg[i].z = tmp_leg[i].z_home;
        }
      }
      if (i == middle_left)
      {
        tmp_leg[i].x = 0.5 * support_hexagon->long_diagonal * cos(-delta_yaw) - 0.5 * tmp_body_state->long_diagonal;
        tmp_leg[i].y = 0.5 * support_hexagon->long_diagonal * sin(-delta_yaw);
        tmp_leg[i].z = tmp_leg[i].z_home - 3 * cos(count * M_PI * 2 * 0.0020125);
        if (tmp_leg[i].z <= tmp_leg[i].z_home)
        {
          tmp_leg[i].z = tmp_leg[i].z_home;
        }
      }
      if (i == front_right)
      {
        tmp_leg[i].x = (0.5 * support_hexagon->long_diagonal * sin((M_PI / 3.0) + delta_yaw) - 0.5 * tmp_body_state->short_diagonal);
        tmp_leg[i].y = (0.5 * support_hexagon->long_diagonal * cos((M_PI / 3.0) + delta_yaw) - 0.5 * tmp_body_state->side);
        tmp_leg[i].z = tmp_leg[i].z_home - 3 * cos(count * M_PI * 2 * 0.0020125);
        if (tmp_leg[i].z <= tmp_leg[i].z_home)
        {
          tmp_leg[i].z = tmp_leg[i].z_home;
        }
      }
    }
  }
}

void set_val_from_controller(leg_state *tmp_leg, js_event event, controler_state *controler, hexapod_body_state *body_state, support_polygon *support_hex)
{
  //コントローラクラスの値をロボットに適用
  double x0, x1;
  double y0, y1;
  int j = front_left;
  //x0,y0は左のジョイスティック（進行方向用）
  //x1,y1は右のジョイスティック(姿勢制御用)
  x0 = (double)controler->axes0_x;
  y0 = (double)controler->axes0_y;

  x1 = (double)controler->axes1_x;
  y1 = (double)controler->axes1_y;

  for (int i = 0; i <= j; i++)
  {
    tmp_leg[i].trajectory_yaw = -(atan2(y0, x0) - (M_PI / 2));
    //printf("trj yaw from joy %f \n", tmp_leg[i].trajectory_yaw);
  }
  for (int i = 0; i <= j; i++)
  {
    tmp_leg[i].trajectory_velocity = (sqrt(pow(abs(x0), 2.0) + pow(abs(y0), 2.0))) / 36000;
  }
  body_state->roll = -(1.5 * M_PI / 18.0) * (x1 / 36000);
  body_state->pitch = (1.5 * M_PI / 18.0) * (y1 / 36000);

  if (controler->A == 1)
  {
    body_state->cog_height = body_state->cog_height + 0.1;
  }
  if (controler->B == 1)
  {
    body_state->cog_height = body_state->cog_height - 0.1;
  }
  if (controler->X)
  {
    support_hex->long_diagonal = support_hex->long_diagonal + 0.1;
    support_hex->short_diagonal = support_hex->long_diagonal * 0.5 * sqrt(3.0);
  }
  if (controler->Y)
  {
    support_hex->long_diagonal = support_hex->long_diagonal - 0.1;
    support_hex->short_diagonal = support_hex->long_diagonal * 0.5 * sqrt(3.0);
  }
  // printf("x:%f y:%f \n", x1, y1);
}

void set_val_from_jy901_and_controller(leg_state *tmp_leg, controler_state *controler, jy901_state *jy901, hexapod_body_state *body_state, PID_parm *PIDpitch, PID_parm *PIDroll)
{
  //コントローラクラスの値をロボットに適用
  double x0, x1;
  double y0, y1;
  int j = front_left;
  double delta_roll;
  double delta_pitch;
  struct timeval currentTime;

  //x0,y0は左のジョイスティック（進行方向用）
  //x1,y1は右のジョイスティック（重心制御）
  x0 = (double)controler->axes0_x;
  y0 = (double)controler->axes0_y;

  x1 = (double)controler->axes1_x;
  y1 = (double)controler->axes1_y;

  for (int i = 0; i <= j; i++)
  {
    tmp_leg[i].trajectory_yaw = -(atan2(y0, x0) - (M_PI / 2));
    //printf("trj yaw from joy %f \n", tmp_leg[i].trajectory_yaw);
  }
  for (int i = 0; i <= j; i++)
  {
    tmp_leg[i].trajectory_velocity = (sqrt(pow(abs(x0), 2.0) + pow(abs(y0), 2.0))) / 36000;
  }

  double p, i, d;
  gettimeofday(&currentTime, NULL);

  //微分のための微小時間の計算
  PIDroll->pastTime = PIDroll->currentTime;
  PIDroll->currentTime = (currentTime.tv_usec) * 0.000001;
  PIDroll->DELTA_T = PIDroll->currentTime - PIDroll->pastTime;
  PIDpitch->DELTA_T = PIDroll->DELTA_T;

  //ロール軸のPID制御
  //偏差の計算
  PIDroll->dif[0] = PIDroll->dif[1];
  PIDroll->dif[1] = 0.0 - jy901->roll;
  //偏差の積分
  //PIDroll->int_err = PIDroll->int_err + PIDroll->dif[1] * PIDroll->DELTA_T;
  PIDroll->int_err = PIDroll->int_err + PIDroll->dif[1] * 0.01;

  p = PIDroll->KP * PIDroll->dif[1];
 // d = PIDroll->KD * (PIDroll->dif[0] - PIDroll->dif[1]) / PIDroll->DELTA_T;
  d = PIDroll->KD * (PIDroll->dif[0] - PIDroll->dif[1]) / 0.01;
  i = PIDroll->KI * PIDroll->int_err;

  // body_state->roll = body_state->roll + p - d;//謎制御
  body_state->roll = p + i - d; //pid制御
  //body_state->roll = p; //p制御

  //ピッチ軸のPD制御
  PIDpitch->dif[0] = PIDpitch->dif[1];
  PIDpitch->dif[1] = 0.0 + jy901->pich;
  //偏差の積分
 // PIDpitch->int_err = PIDpitch->int_err + PIDpitch->dif[1] * PIDroll->DELTA_T;
 PIDpitch->int_err = PIDpitch->int_err + PIDpitch->dif[1] * 0.01;

  p = PIDpitch->KP * PIDpitch->dif[1];
  //d = PIDpitch->KD * (PIDpitch->dif[0] - PIDpitch->dif[1]) / PIDpitch->DELTA_T;
  d = PIDpitch->KD * (PIDpitch->dif[0] - PIDpitch->dif[1]) / 0.01;
  i = PIDpitch->KI * PIDpitch->int_err;

  //body_state->pitch = body_state->pitch * 2 + p - d;//謎制御
  body_state->pitch = p + i - d; //pi制御
  printf("%f",d);
  //body_state->pitch = p; //p制御

  body_state->ZMP_y = 5.0 * (y1 / 36000.0);
  body_state->ZMP_x = 5.0 * (x1 / 36000.0);
  if (controler->A == 1)
  {
    body_state->cog_height = body_state->cog_height + 0.1;
  }
  if (controler->B == 1)
  {
    body_state->cog_height = body_state->cog_height - 0.1;
  }
  // if (controler->Y == 1)
  // {
  //   for (int i = 0; i <= j; i++)
  //   {
  //     tmp_leg[i].trajectory_hight = tmp_leg[i].trajectory_hight + 0.05;
  //   }
  // }
  // if (controler->X == 1)
  // {
  //   for (int i = 0; i <= j; i++)
  //   {
  //     tmp_leg[i].trajectory_hight = tmp_leg[i].trajectory_hight - 0.05;
  //   }
  // }
}
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
int main(int argc, char *argv[])
{
  ///////////////////////コントローラ関係/////////////////////
  int fd = open("/dev/input/js0", O_NONBLOCK); //初期化
  struct js_event event;
  ////////////////////////dynamixedl関係/////////////////////
  const char *port_name = "/dev/ttyUSB0";
  int baud_rate = 2 * 1000 * 1000;
  uint16_t model_number = 0;
  uint8_t dxl_id[18];

  dxl_id[0] = 1;
  dxl_id[1] = 2;
  dxl_id[2] = 3;
  dxl_id[3] = 4;
  dxl_id[4] = 5;
  dxl_id[5] = 6;
  dxl_id[6] = 7;
  dxl_id[7] = 8;
  dxl_id[8] = 9;
  dxl_id[9] = 10;
  dxl_id[10] = 11;
  dxl_id[11] = 12;
  dxl_id[12] = 13;
  dxl_id[13] = 14;
  dxl_id[14] = 15;
  dxl_id[15] = 16;
  dxl_id[16] = 17;
  dxl_id[17] = 18;

  bool result = false;
  port_name = "/dev/ttyUSB0";
  const char *log;

  result = dxl_wb.init(port_name, baud_rate, &log);
  if (result == false)
  {
    printf("%s\n", log);
    printf("Failed to init\n");
    return 0;
  }
  else
    printf("Succeed to init(%d)\n", baud_rate);

  //pingを使って通信を確認
  for (int cnt = 0; cnt <= 17; cnt++)
  {
    result = dxl_wb.ping(dxl_id[cnt], &model_number, &log);
    if (result == false)
    {
      printf("%s\n", log);
      printf("Failed to ping\n");
    }
    else
    {
      printf("Succeeded to ping\n");
      printf("id : %d, model_number : %d\n", dxl_id[cnt], model_number);
    }
    result = dxl_wb.jointMode(dxl_id[cnt], 0, 0, &log);
    if (result == false)
    {
      printf("%s\n", log);
      printf("Failed to change joint mode\n");
    }
    else
    {
      printf("Succeed to change joint mode\n");
    }
  }

  result = dxl_wb.initBulkWrite(&log);
  if (result == false)
  {
    printf("%s\n", log);
  }
  else
  {
    printf("%s\n", log);
  }

  result = dxl_wb.initBulkRead(&log);
  if (result == false)
  {
    printf("%s\n", log);
  }
  else
  {
    printf("%s\n", log);
  }

  result = dxl_wb.addBulkReadParam(dxl_id[0], "Present_Position", &log);

  if (result == false)
  {
    printf("%s\n", log);
    printf("Failed to add bulk read position param\n");
  }
  else
  {
    printf("%s\n", log);
  }
  ///////////////////ロボットの要素//////////////////////////
  double count = 0.0;
  controler_state *controler;
  PID_parm PIDpitch[1];
  PID_parm PIDroll[1];
  controler = (controler_state *)malloc(sizeof(controler_state));
  hexapod_body_state body_state[1];
  support_polygon support_hexagon[1];
  leg_state leg[6];
  jy901_state jy901[1];
  jy901_state terrainJy[1];

  //////////////////ロボット搭載のjy901関係の初期設定//////////////////////
  int serial_port = open("/dev/ttyUSB1", O_RDWR);
  // Create new termios struc, we call it 'tty' for convention
  struct termios tty;
  memset(&tty, 0, sizeof tty);

  // Read in existing settings, and handle any error

  if (tcgetattr(serial_port, &tty) != 0)
  {
    printf("Error %i from tcgetattr: %s\n", errno, strerror(errno));
  }

  tty.c_cflag &= ~PARENB;        // Clear parity bit, disabling parity (most common)
  tty.c_cflag &= ~CSTOPB;        // Clear stop field, only one stop bit used in communication (most common)
  tty.c_cflag |= CS8;            // 8 bits per byte (most common)
  tty.c_cflag &= ~CRTSCTS;       // Disable RTS/CTS hardware flow control (most common)
  tty.c_cflag |= CREAD | CLOCAL; // Turn on READ & ignore ctrl lines (CLOCAL = 1)

  tty.c_lflag &= ~ICANON;
  tty.c_lflag &= ~ECHO;                                                        // Disable echo
  tty.c_lflag &= ~ECHOE;                                                       // Disable erasure
  tty.c_lflag &= ~ECHONL;                                                      // Disable new-line echo
  tty.c_lflag &= ~ISIG;                                                        // Disable interpretation of INTR, QUIT and SUSP
  tty.c_iflag &= ~(IXON | IXOFF | IXANY);                                      // Turn off s/w flow ctrl
  tty.c_iflag &= ~(IGNBRK | BRKINT | PARMRK | ISTRIP | INLCR | IGNCR | ICRNL); // Disable any special handling of received bytes

  tty.c_oflag &= ~OPOST; // Prevent special interpretation of output bytes (e.g. newline chars)
  tty.c_oflag &= ~ONLCR; // Prevent conversion of newline to carriage return/line feed
  // tty.c_oflag &= ~OXTABS; // Prevent conversion of tabs to spaces (NOT PRESENT ON LINUX)
  // tty.c_oflag &= ~ONOEOT; // Prevent removal of C-d chars (0x004) in output (NOT PRESENT ON LINUX)

  tty.c_cc[VTIME] = 10; // Wait for up to 1s (10 deciseconds), returning as soon as any data is received.
  tty.c_cc[VMIN] = 0;

  // Set in/out baud rate to be 115200
  cfsetispeed(&tty, B115200);
  cfsetospeed(&tty, B115200);

  if (tcsetattr(serial_port, TCSANOW, &tty) != 0)
  {
    printf("Error %i from tcsetattr: %s\n", errno, strerror(errno));
  }

  //////////////////実験フィールド状態記録用のjy901関係の初期設定//////////////////////
  int tr_serial_port = open("/dev/ttyUSB2", O_RDWR);
  // Create new termios struc, we call it 'tty' for convention
  struct termios tr_tty;
  memset(&tty, 0, sizeof tr_tty);

  // Read in existing settings, and handle any error

  if (tcgetattr(serial_port, &tr_tty) != 0)
  {
    printf("Error %i from tcgetattr: %s\n", errno, strerror(errno));
  }

  tr_tty.c_cflag &= ~PARENB;        // Clear parity bit, disabling parity (most common)
  tr_tty.c_cflag &= ~CSTOPB;        // Clear stop field, only one stop bit used in communication (most common)
  tr_tty.c_cflag |= CS8;            // 8 bits per byte (most common)
  tr_tty.c_cflag &= ~CRTSCTS;       // Disable RTS/CTS hardware flow control (most common)
  tr_tty.c_cflag |= CREAD | CLOCAL; // Turn on READ & ignore ctrl lines (CLOCAL = 1)

  tr_tty.c_lflag &= ~ICANON;
  tr_tty.c_lflag &= ~ECHO;                                                        // Disable echo
  tr_tty.c_lflag &= ~ECHOE;                                                       // Disable erasure
  tr_tty.c_lflag &= ~ECHONL;                                                      // Disable new-line echo
  tr_tty.c_lflag &= ~ISIG;                                                        // Disable interpretation of INTR, QUIT and SUSP
  tr_tty.c_iflag &= ~(IXON | IXOFF | IXANY);                                      // Turn off s/w flow ctrl
  tr_tty.c_iflag &= ~(IGNBRK | BRKINT | PARMRK | ISTRIP | INLCR | IGNCR | ICRNL); // Disable any special handling of received bytes

  tr_tty.c_oflag &= ~OPOST; // Prevent special interpretation of output bytes (e.g. newline chars)
  tr_tty.c_oflag &= ~ONLCR; // Prevent conversion of newline to carriage return/line feed
  // tty.c_oflag &= ~OXTABS; // Prevent conversion of tabs to spaces (NOT PRESENT ON LINUX)
  // tty.c_oflag &= ~ONOEOT; // Prevent removal of C-d chars (0x004) in output (NOT PRESENT ON LINUX)

  tr_tty.c_cc[VTIME] = 10; // Wait for up to 1s (10 deciseconds), returning as soon as any data is received.
  tr_tty.c_cc[VMIN] = 0;

  // Set in/out baud rate to be 115200
  cfsetispeed(&tr_tty, B115200);
  cfsetospeed(&tr_tty, B115200);

  if (tcsetattr(tr_serial_port, TCSANOW, &tr_tty) != 0)
  {
    printf("Error %i from tcsetattr: %s\n", errno, strerror(errno));
  }
  ///////////////////実験データ記録ファイルのための準備//////////////////////////////////////////
  FILE *jyRecFile;
  jyRecFile = fopen("jyRec.txt", "w");
  fprintf(jyRecFile, "Kp= %f,Kd =%f \n", PIDpitch->KP, PIDpitch->KD);
  fprintf(jyRecFile, "stride = %f, trjHeight = %f,body_heigut %f\n", leg[front_left].trajectory_width * 2, leg[front_left].trajectory_hight, body_state->cog_height);
  fprintf(jyRecFile, "POSIXtime,terrainPitch,terrainroll,jyPitch,jyRoll,estimateTerrainPich,estimateTerrainRoll\n");
  struct timeval currentTime; //現在時刻を格納する構造体変数

  //メインのループ，拡張したいときはここを中心にいじる
  while (controler->start == 0)
  {

    //コントローラからの値の読み込み
    read(fd, &event, sizeof(event));
    write_controler_state(controler, event);
    if (controler->back == 1 && body_state->mode == auto_attitude_mode && body_state->mode_is_alrdy_changed == 0)
    {
      body_state->mode = manualMode;
      body_state->mode_is_alrdy_changed = 1;
    }

    if (controler->back == 1 && body_state->mode == manualMode && body_state->mode_is_alrdy_changed == 0)
    {
      body_state->mode = auto_attitude_mode;
      body_state->mode_is_alrdy_changed = 1;
    }

    if (controler->back == 0)
    {
      body_state->mode_is_alrdy_changed = 0;
    }
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

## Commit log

2020-01-23 Reorganized repository structure.
    [436450500.ipt, 436450500.stp, 436500513.ipt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]
2020-01-23 Added auto balancer with gyro sensor
2020-02-11 Remove "Computer" from main assembly, Add UCS on each assembly.
    [DC11_A01_CASE_CVR_DUMMY.ipt, DC11_A01_CASE_CVR_DUMMY_MIR.ipt, DC11_A01_CASE_CVR_DUMMY_mir1.ipt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]
2021-05-29 Update parts numbering
    [00_000_HAPTHEXA_R3.iam, 00_002_SINGLE_LEG_R1.iam, 00_003_COXA_R1.iam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]

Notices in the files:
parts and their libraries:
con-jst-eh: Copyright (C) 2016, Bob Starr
